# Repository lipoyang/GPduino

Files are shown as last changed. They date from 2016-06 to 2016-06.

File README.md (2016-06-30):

GPduino
=========

## 概要
GPduinoは、Arduino+Konashi互換のBLEラジコン制御ボードです。  
GPduinoに関する詳細は、[GPduino特設ページ](http://lipoyang.net/gpduino)をごらんください。  
GPduinoの回路/基板設計データとプリセットファームウェアのソースをここに公開します。

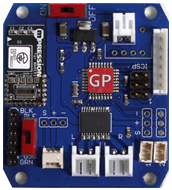
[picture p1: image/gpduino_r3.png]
GPduinoの写真
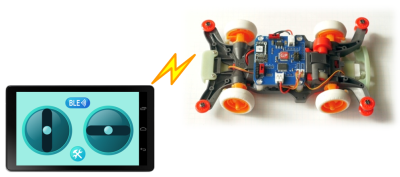
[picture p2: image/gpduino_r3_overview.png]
概要の図
　　　　　

## ファイル一覧

* firm/GPduinoR3/ : ファームウェア(Arduino Pro Mini 3.3V 互換のスケッチ)
* hard/GPduinoPCB/
	* GPduino.sch/brd: 回路/基板設計データ(Eagle形式)
	* GPduino.pdf: 回路図(PDF)
	* GPduino_BOM.xlsx: BOMリスト(Excel形式)
	* GPduino.GBL/GBO/GBP/GBS/GML/GTL/GTO/GTP/GTS/TXT: ガーバデータ
* LICENSE: Apache Licence 2.0です。
	* ただし、回路/基板設計は、Creative Commons Attribution Share-Alike 3.0です。
* README.md これ

## ブートローダの書き込み
部品実装したGPduino基板をArduinoとして使用できるようにするには、まずブートローダを書き込みます。
* ISPコネクタ（CN12）にISPプログラマーを接続します。向きに注意してください。
	* 3.3V系のArduino (Arduino Pro Mini 3.3V版など)をISPプログラマーにすることができます。
	* File > Examples > Arduino ISP をArduinoに書き込んでください。
* Arduino IDEにて、Tools > Board で、Arduino Pro or Pro Mini を選びます。
* Tools > Processor で、ATmega328(3.3V, 8MHz) を選びます。
* Tools > Programmer で、ISPプログラマーを選びます。
	* 上記の、Arduinoを使ったISPプログラマーの場合は、Arduino as ISPを選んでください。
* Tools > Burn Bootloader で、ブートローダーを書き込みます。

## ファームウェアの書き込み
GPduinoは、Arduino Pro Mini 3.3V版互換機です。
* 書き込みはArduino Pro Miniと同様、USBシリアル変換基板が必要です。CN13に接続してください。
	* SparkFun製 FTDI Basic Breakout - 3.3V を推奨します。かならず、3.3Vのものを使用してください。
* 基板のジャンパJ3を[USB]側に設定してください。
* Arduino IDEにて、Tools > Board で、Arduino Pro or Pro Mini を選びます。
* Tools > Processor で、ATmega328(3.3V, 8MHz) を選びます。
* Tools > Port で、USBシリアルのポート番号を選びます。
* Uploadボタンで、ファームウェアを書き込みます。

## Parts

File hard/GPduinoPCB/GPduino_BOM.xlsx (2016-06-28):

GPduino BOM
基板本体
No | Reference | Part Number | Vender | Description | DNP | Qty | Unit Price | Price | Lot Size | Supplier | Supplier Code
1 | C1 | 47u(3216) | (generic) | 3216型 |  | 1 | 30 | 30 | 10 | 秋月 | P-06040
2 | C2 | 10u(3216) | (generic) | 3216型 |  | 1 | 12.5 | 12.5 | 10 | 秋月 | P-06462
3 | C3,4,5,6,7 | 0.1u(1608) | (generic) | 1608型 |  | 4 | 0.325 | 1.3 | 4000 | 秋月 | P-01299
4 | CN1,2 | S2B-EH | JST | EH 2極 L型ポスト | DNP | 0 | 16 | 0 | 1 | 共立 | -
5 | CN3 | B6B-EH-A | JST | EH 6極 I型ポスト | DNP | 0 | 27 | 0 | 1 | 共立 | -
6 | CN4 | S2B-PH-K-S | JST | PH 2極 L型ポスト |  | 1 | 16 | 16 | 1 | 共立 | -
7 | CN5 | B4B-EH-A | JST | EH 4極 I型ポスト | DNP | 0 | 21 | 0 | 1 | 共立 | -
8 | CN6 | 53048-0310 | Molex | PicoBlade 3極 L型ポスト | DNP (部品は付属) | 1 | 45 | 45 | 5 | RS | 319-1092
9 | CN7,8 | 53047-0310 | Molex | PicoBlade 3極 I型ポスト | DNP | 0 | 29 | 0 | 5 | RS | 319-1064
10 | CN9 | - | (generic) | ピンヘッダ 3ピン | DNP (部品は付属) | 1 | 35 | 35 | 16 | 共立 | -
11 | CN10,11 | - | (generic) | ピンヘッダ 3ピン | DNP | 0 | 17 | 0 | 12 | 共立 | -
12 | CN12 | - | (generic) | ピンヘッダ 2×3ピン I型 | DNP | 0 | 70 | 0 | 1 | 共立 | -
13 | CN13 | 0 | (generic) | ピンヘッダ 6ピン I型 | DNP (部品は付属) | 1 | 70 | 70 | 8 | 共立 | -
14 | J3,SW1 | SS-12SDP2 | NKK | スライドスイッチ | DNP (部品は付属) | 2 | 66 | 132 | 1 | 共立 | 391139
15 | R1,2,3 | 10k(1608) | (generic) | 1608型 |  | 3 | 0.2 | 0.6 | 2500 | 秋月 | R-06103
16 | U1 | TC1262-3.3VDB05MP | Microchip | LDO, 3.3V-0.5A, SOT-223型 |  | 1 | 81 | 81 | 1 | RS | 703-7905
17 | U2 | TB6621FNG | Toshiba | Dual DCモータドライバ |  | 1 | 306 | 306 | 1 | RS | 770-3797
18 | U3 | ATmega328P-AU | Atmel | AVRマイコン |  | 1 | 367 | 367 | 1 | RS | 696-3092
19 | U4 | Koshian | Macnica | BLEモジュール |  | 1 | 980 | 980 | 1 | Macnica | -
20 | X1 | CSTCE8M00G55-R0 | Murata | セラロック 8MHz |  | 1 | 45 | 45 | 10 | RS | 721-4821
21 | - | - | FusionPCB | 基板 |  | 1 | 241.7 | 241.7 | 10 | FusionPCB | -
22 | - | PH2P300L | Marutsu | PH 2極 アッセンブルケーブル |  | 1 | 54 | 54 | 1 | マルツ | -
 |  |  |  |  |  |  | Total | 2417.1

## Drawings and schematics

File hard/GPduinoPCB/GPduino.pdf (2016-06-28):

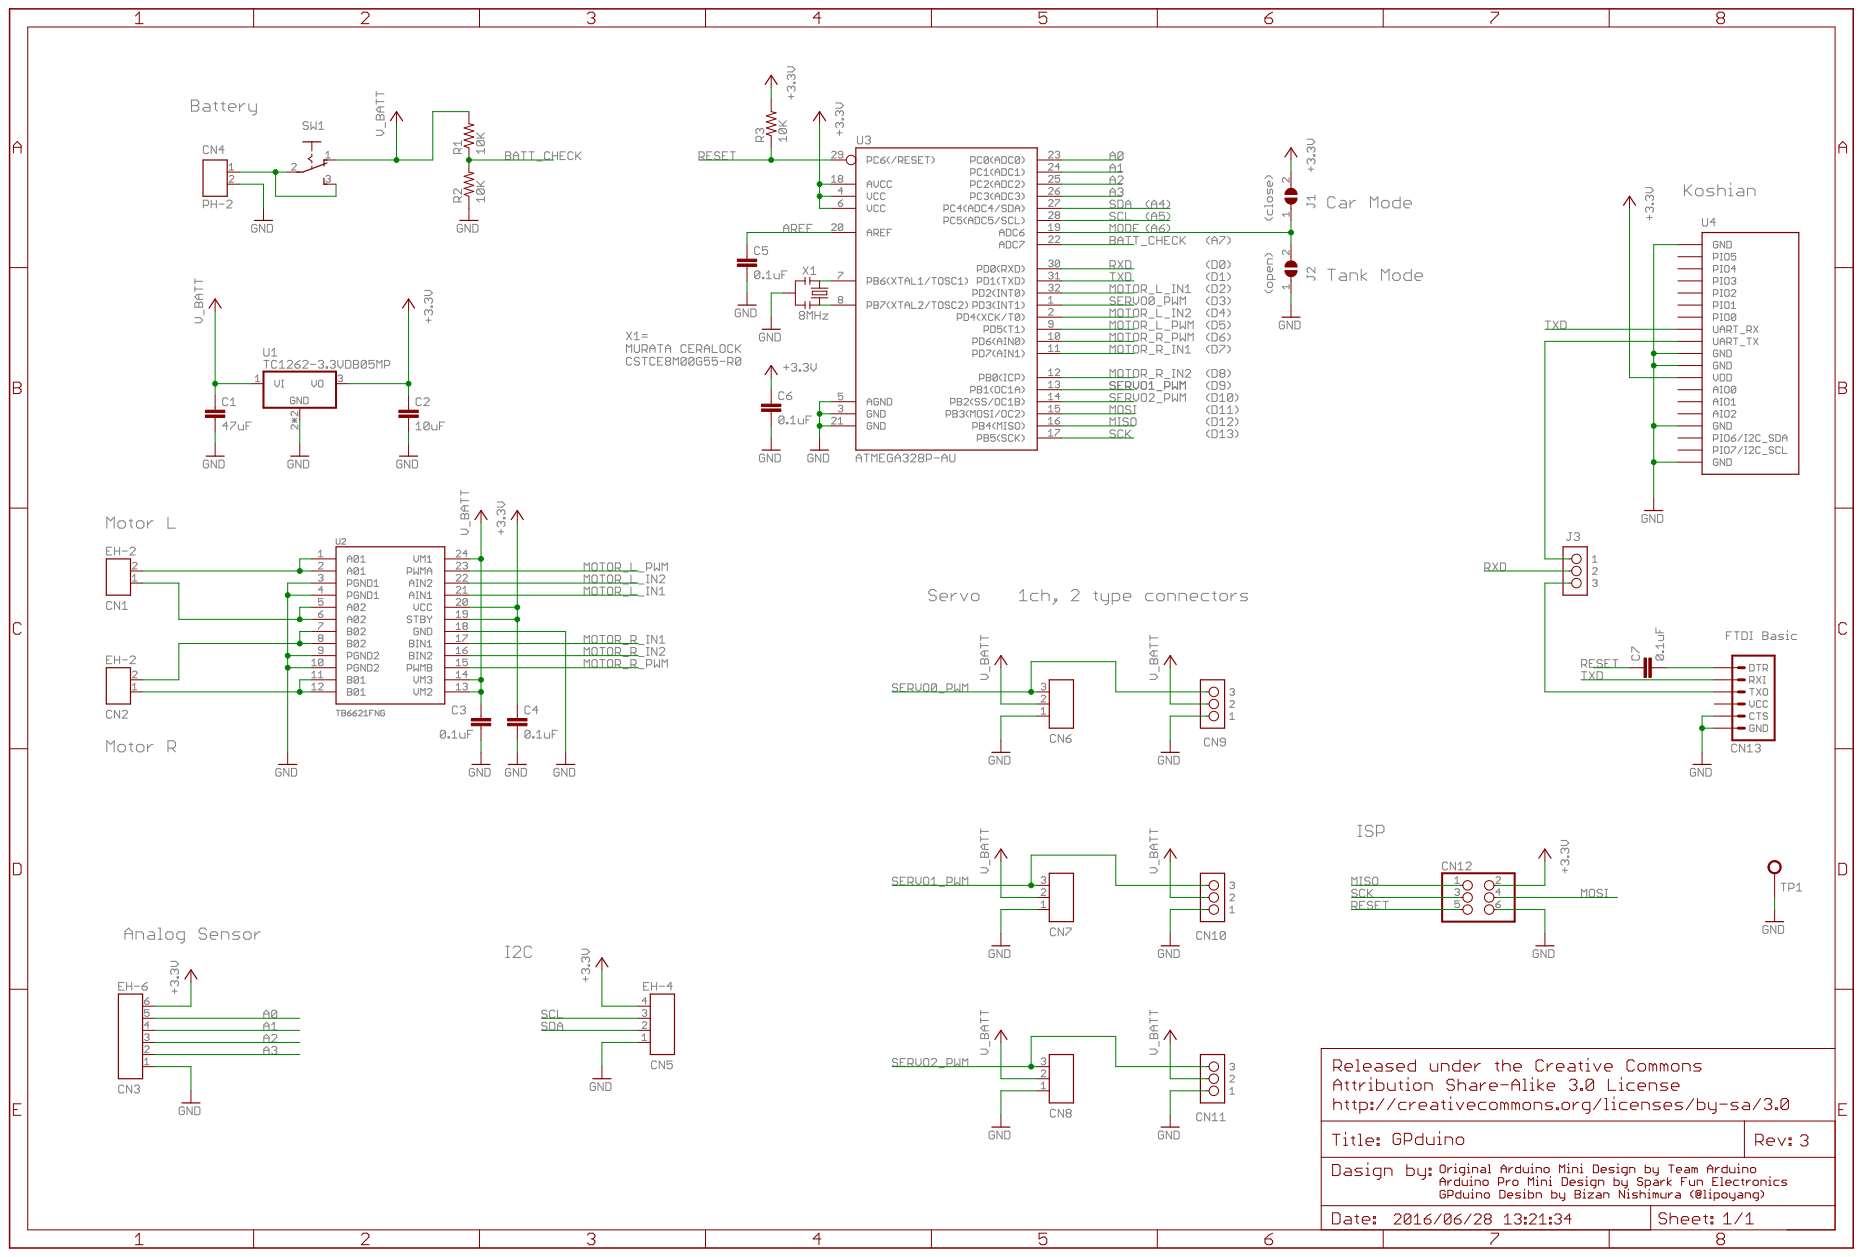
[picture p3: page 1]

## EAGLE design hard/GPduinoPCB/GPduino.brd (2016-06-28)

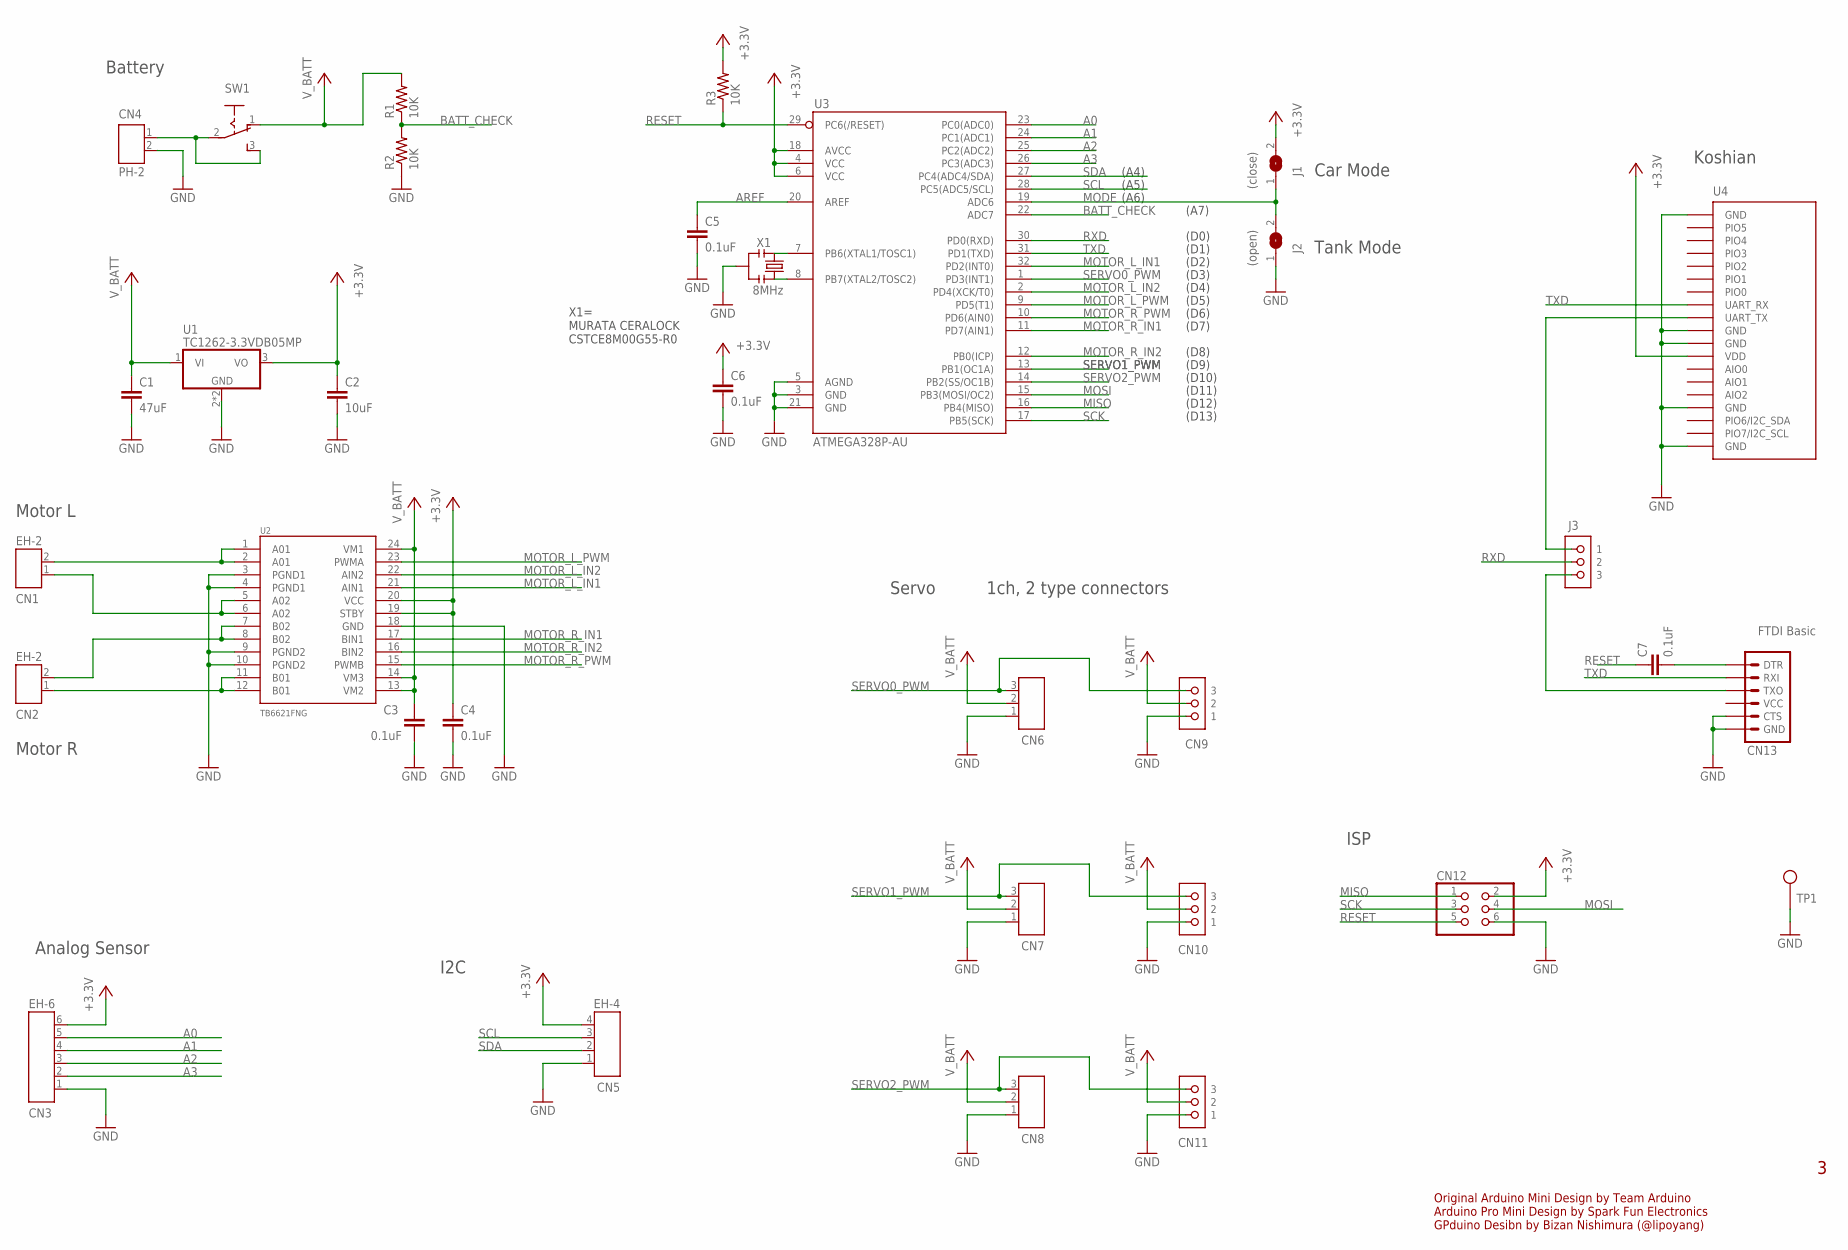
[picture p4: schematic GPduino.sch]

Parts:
C1: 47uF; C3216
C2: 10uF; C3216
C3, C4, C5, C6, C7: 0.1uF; C1608
CN1, CN2: EH-2
CN3: EH-6
CN4: PH-2
CN5: EH-4
CN6, CN7, CN8: PICOBLADE-3
CN9, CN10, CN11: cn6; CON_RC_SERVO
CN12: CN9; 2X03
CN13: FTDI Basic; 1X06
J1: (close); SJ
J2: (open); SJ
J3: XX-2; JUMPER_PIN_1X3
R1, R2, R3: 10K; 0603-RES
SW1: SW1; SLIDE-SW
TP1: TEST_PIN
U1: TC1262-3.3VDB05MP; SOT223
U2: TB6621FNG; SSOP24
U3: ATMEGA328P-AU; TQFP32-08
U4: KOSHIAN
X1: 8MHz; RESONATOR-SMD-1:1

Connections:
+3V3: C2.1, C4.1, C6.1, CN3.6, CN5.4, CN12.2, J1.2, R3.2, U1.3 (VO), U2.19 (STBY), U2.20 (VCC), U3.4 (VCC), U3.6 (VCC), U3.18 (AVCC), U4.12 (VDD)
A0: CN3.5, U3.23 (PC0(ADC0))
A01: CN1.2, U2.1 (A01), U2.2 (A01)
A1: CN3.4, U3.24 (PC1(ADC1))
A02: CN1.1, U2.5 (A02), U2.6 (A02)
A2: CN3.3, U3.25 (PC2(ADC2))
A3: CN3.2, U3.26 (PC3(ADC3))
AREF: C5.1, U3.20 (AREF)
BATT_CHECK: R1.1, R2.2, U3.22 (ADC7)
GND: C1.2, C2.2, C3.2, C4.2, C5.2, C6.2, CN3.1, CN4.2, CN5.1, CN6.1, CN7.1, CN8.1, CN9.1, CN10.1, CN11.1, CN12.6, CN13.5 (CTS), CN13.6 (GND), J2.1, R2.1, TP1.1, U1.2 (GND), U1.4 (GND), U2.3 (PGND1), U2.4 (PGND1), U2.9 (PGND2), U2.10 (PGND2), U2.18 (GND), U3.3 (GND), U3.5 (AGND), U3.21 (GND), U4.1 (GND), U4.10 (GND), U4.11 (GND), U4.16 (GND), U4.16@2 (GND), U4.20 (GND), X1.2
MISO: CN12.1, U3.16 (PB4(MISO))
MODE: J1.1, J2.2, U3.19 (ADC6)
MOSI: CN12.4, U3.15 (PB3(MOSI/OC2))
MOTOR_L_IN1: U2.21 (AIN1), U3.32 (PD2(INT0))
MOTOR_L_IN2: U2.22 (AIN2), U3.2 (PD4(XCK/T0))
MOTOR_L_PWM: U2.23 (PWMA), U3.9 (PD5(T1))
MOTOR_R_IN1: U2.17 (BIN1), U3.11 (PD7(AIN1))
MOTOR_R_IN2: U2.16 (BIN2), U3.12 (PB0(ICP))
MOTOR_R_PWM: U2.15 (PWMB), U3.10 (PD6(AIN0))
unnamed: CN4.1, SW1.2, SW1.3 (S)
unnamed: U3.8 (PB7(XTAL2/TOSC2)), X1.3
unnamed: U3.7 (PB6(XTAL1/TOSC1)), X1.1
unnamed: CN2.1, U2.11 (B01), U2.12 (B01)
unnamed: CN2.2, U2.7 (B02), U2.8 (B02)
unnamed: J3.1, U4.9 (UART_TX)
unnamed: C7.2, CN13.1 (DTR)
unnamed: CN13.3 (TXO), J3.3
RESET: C7.1, CN12.5, R3.1, U3.29 (PC6(/RESET))
RXD: J3.2, U3.30 (PD0(RXD))
SCK: CN12.3, U3.17 (PB5(SCK))
SCL: CN5.3, U3.28 (PC5(ADC5/SCL))
SDA: CN5.2, U3.27 (PC4(ADC4/SDA))
SERVO0_PWM: CN6.3, CN9.3, U3.1 (PD3(INT1))
SERVO1_PWM: CN7.3, CN10.3, U3.13 (PB1(OC1A))
SERVO2_PWM: CN8.3, CN11.3, U3.14 (PB2(SS/OC1B))
TXD: CN13.2 (RXI), U3.31 (PD1(TXD)), U4.8 (UART_RX), U4.8@2 (UART_RX)
V_BATT: C1.1, C3.1, CN6.2, CN7.2, CN8.2, CN9.2, CN10.2, CN11.2, R1.2, SW1.1 (O), U1.1 (VI), U2.13 (VM2), U2.14 (VM3), U2.24 (VM1)

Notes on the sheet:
Battery
Servo
Motor L
Original Arduino Mini Design by Team Arduino Arduino Pro Mini Design by Spark Fun Electronics GPduino Desibn by Bizan Nishimura (@lipoyang)
1ch, 2 type connectors
Analog Sensor
Motor R
ISP
Koshian
X1= MURATA CERALOCK CSTCE8M00G55-R0
Car Mode
Tank Mode
(D0)
(D1)
(D2)
(D3)
(D4)
(D5)
(D6)
(D7)
(D8)
(D9)
(D10)
(D11)
(D12)
(D13)
(A7)
(A6)
(A5)
(A4)
I2C

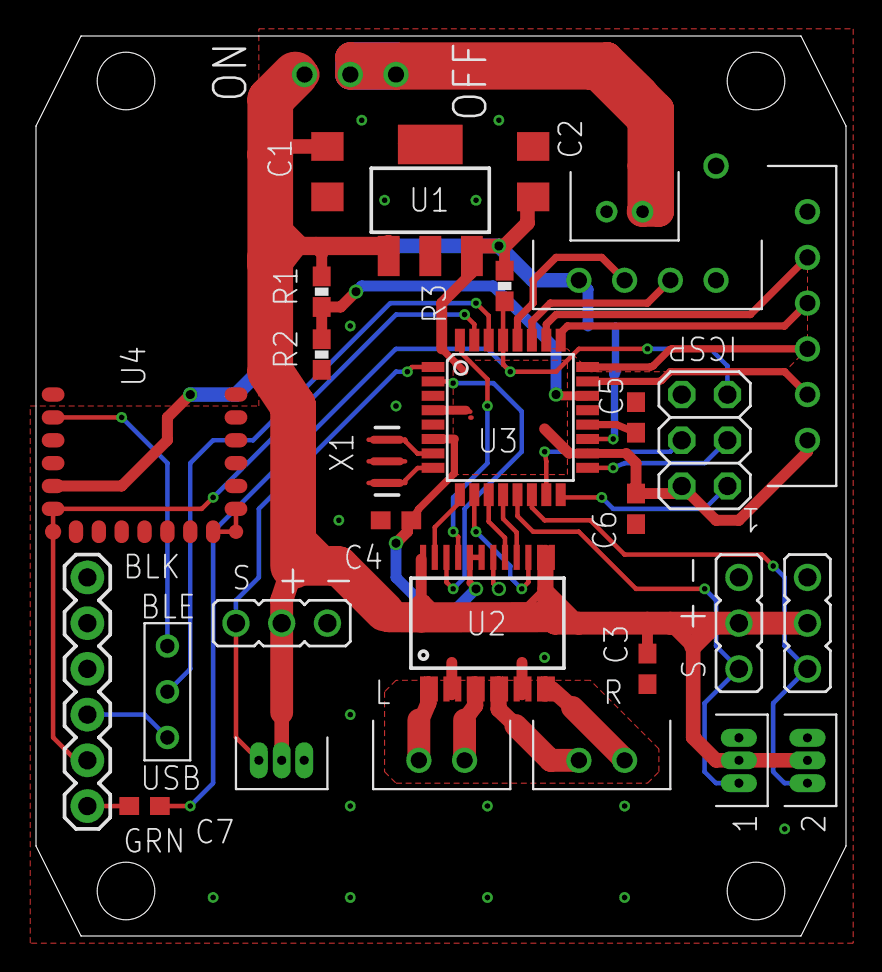
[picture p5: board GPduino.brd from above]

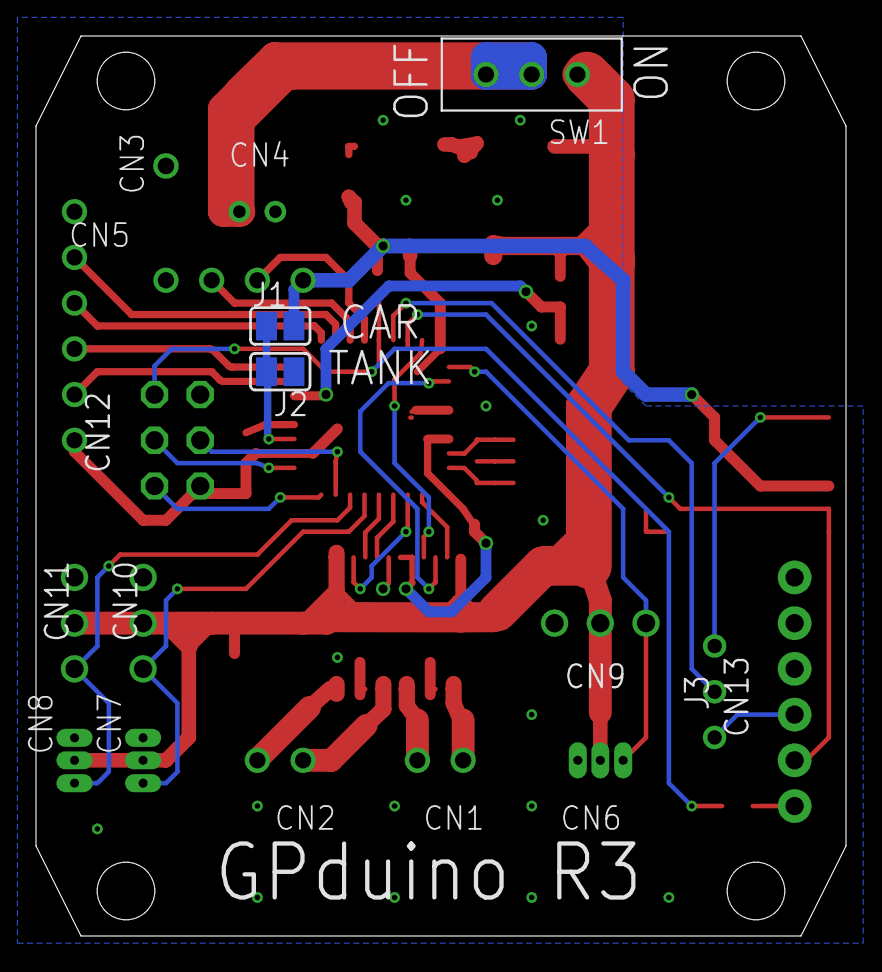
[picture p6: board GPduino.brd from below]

Board: 2 copper layers, 45.0 x 50.0 mm, 33 parts (3 on the bottom side), 37 nets.

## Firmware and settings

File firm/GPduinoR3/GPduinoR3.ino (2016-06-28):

/*
This software is available under NYSL(Nirunari Yakunari Sukinishiro License).
*/

#include <Servo.h>
#include <EEPROM.h>
#include "common.h"
#include "MovingAverage.h"

// ピン番号 (デジタル)
#define MOTOR_L_IN1    2
#define SERVO0_PWM     3
#define MOTOR_L_IN2    4
#define MOTOR_L_PWM    5
#define MOTOR_R_PWM    6
#define MOTOR_R_IN1    7
#define MOTOR_R_IN2    8
#define SERVO1_PWM     9
#define SERVO2_PWM     10

// ピン番号 (アナログ)
#define ANALOG_0      0
#define ANALOG_1      1
#define ANALOG_2      2
#define ANALOG_3      3
#define MODE_CHECK    6
#define BATT_CHECK    7

// サーボ
Servo servo[3];

// バッテリー電圧チェック
MovingAverage Vbat_MovingAve;

// モード
static int drive_mode;
#define MODE_TANK   0   // 戦車モード
#define MODE_CAR    1   // 自動車モード

// 戦車モードのプロポ状態保持用
static int g_fb;  // 前後方向
static int g_lr;  // 左右方向

// 暴走チェックカウンタ
static int cnt_runaway;

// 3.3V未満でローバッテリーとする
// (3.3V / 2) / 3.3V * 1024 =  512
#define LOW_BATTERY    512

// 四輪操舵のモード
static int g_steer_pol_f;
static int g_steer_pol_b;

// サーボの調整
static int g_servo_pol[3]; // 極性
static int g_servo_ofs[3]; // オフセット
static int g_servo_amp[3]; // 振幅

// 送信バッファ
static char txbuff[256];

/**
 * バッテリー電圧チェック
 */
void battery_check()
{
    static int cnt = 0;
    
    unsigned short Vbat = analogRead(BATT_CHECK);
    unsigned short Vbat_ave = Vbat_MovingAve.pop(Vbat);
    
    // 1秒ごとに電圧値送信
    cnt++;
    if(cnt >= 1000)
    {
        cnt=0;
        
        txbuff[0]='#';
        txbuff[1]='B';
        Uint16ToHex(&txbuff[2], Vbat_ave, 3);
        txbuff[5]='$';
        txbuff[6]='\0';
        Serial.print(txbuff);
    }
    
    // 電圧が低下したら停止
    if(Vbat_ave < LOW_BATTERY){
        // モータ停止
        analogWrite(MOTOR_L_PWM, 0);
        analogWrite(MOTOR_R_PWM, 0);
        digitalWrite(MOTOR_L_IN1, LOW);
        digitalWrite(MOTOR_L_IN2, LOW);
        digitalWrite(MOTOR_R_IN1, LOW);
        digitalWrite(MOTOR_R_IN2, LOW);
        // 復帰しない
        while(true){
            ;
        }
    }
}

/**
 * 暴走チェック
 */
void runaway_check()
{
    cnt_runaway++;
    
    // 1秒間コマンドが来なければモータ停止
    if(cnt_runaway > 1000)
    {
      analogWrite(MOTOR_L_PWM, 0);
      analogWrite(MOTOR_R_PWM, 0);
      digitalWrite(MOTOR_L_IN1, LOW);
      digitalWrite(MOTOR_L_IN2, LOW);
      digitalWrite(MOTOR_R_IN1, LOW);
      digitalWrite(MOTOR_R_IN2, LOW);
    }
}

/*
 * サーボの初期化
 */
void servo_init()
{
    int i;
    if(EEPROM.read(0) == 0xA5){
        for(i=0;i<3;i++){
            g_servo_pol[i] = (int)((signed char)EEPROM.read(i*3 + 1));
            g_servo_ofs[i] = (int)((signed char)EEPROM.read(i*3 + 2));
            g_servo_amp[i] =                    EEPROM.read(i*3 + 3);
        }
    }else{
        EEPROM.write(0, 0xA5);
        for(i=0;i<3;i++){
            g_servo_pol[i] = 1;
            g_servo_ofs[i] = 0;
            g_servo_amp[i] = 90;
            EEPROM.write(i*3 + 1, g_servo_pol[i]);
            EEPROM.write(i*3 + 2, g_servo_ofs[i]);
            EEPROM.write(i*3 + 3, g_servo_amp[i]);
        }
    }
    servo[0].attach(SERVO0_PWM);
    servo[1].attach(SERVO1_PWM);
    servo[2].attach(SERVO2_PWM);
    servo_ctrl(0,0);
    servo_ctrl(1,0);
    servo_ctrl(2,0);
}

/*
 * サーボ制御
 */
void servo_ctrl(int ch, int val)
{
    int deg = 90 + ((val + g_servo_ofs[ch]) *  g_servo_amp[ch]) / 127 * g_servo_pol[ch];
    
    // sprintf(txbuff, "%4d %4d / %4d %4d %4d", val, deg, g_servo_ofs[ch], g_servo_amp[ch], g_servo_pol[ch]);
    // Serial.println(txbuff);
    
    servo[ch].write(deg);
}

// 初期設定
void setup() {
    // シリアル通信の設定
    SerialCom_init();

    // PWMの初期化
    analogWrite(MOTOR_L_PWM, 0);
    analogWrite(MOTOR_R_PWM, 0);
    
    // GPIOの初期化
    digitalWrite(MOTOR_L_IN1, LOW);
    digitalWrite(MOTOR_L_IN2, LOW);
    digitalWrite(MOTOR_R_IN1, LOW);
    digitalWrite(MOTOR_R_IN2, LOW);
    pinMode(MOTOR_L_IN1, OUTPUT);
    pinMode(MOTOR_L_IN2, OUTPUT);
    pinMode(MOTOR_R_IN1, OUTPUT);
    pinMode(MOTOR_R_IN2, OUTPUT);
    
    // モード判定
    int mode_check = analogRead( MODE_CHECK );
    drive_mode = (mode_check > 512) ? MODE_CAR : MODE_TANK;

    if(drive_mode == MODE_CAR){
        // サーボの初期化
        servo_init();
    }
    
    // 変数初期化
    g_fb = 0;
    g_lr = 0;
    cnt_runaway = 0;
    Vbat_MovingAve.init();
    g_steer_pol_f = 1;
    g_steer_pol_b = 0;
}

// メインループ
void loop() {
    
    // シリアル受信
    SerialCom_loop();
    // バッテリー電圧チェック
    battery_check();
    // 暴走チェック
    runaway_check();
    
    delay(1);
}

/*
 * モータの制御
 */
void ctrl_motor(int ch, int val)
{
    static const int IN1[]={MOTOR_L_IN1, MOTOR_R_IN1};
    static const int IN2[]={MOTOR_L_IN2, MOTOR_R_IN2};
    static const int PWM[]={MOTOR_L_PWM, MOTOR_R_PWM};
    
    int l,r;
    int lpwm,rpwm,lin1,lin2,rin1,rin2;
    
    int pwm = (abs(val) << 1) + 1;
    if(pwm<0) pwm = 0;
    if(pwm>255) pwm = 255;
    
    int in1,in2;
    if(val > 0){
        in1 = LOW;
        in2 = HIGH;
    }else if(val < 0){
        in1 = HIGH;
        in2 = LOW;
    }else{
        in1 = LOW;
        in2 = LOW;
        pwm = 0;
    }

    digitalWrite(IN1[ch], in1);
    digitalWrite(IN2[ch], in2);
    analogWrite(PWM[ch], pwm);
}

/**
 * 戦車のモータ制御
 */
void ctrl_tank()
{
    int l,r;
    int lpwm,rpwm,lin1,lin2,rin1,rin2;
    
    r = (int)(g_fb - g_lr/2);
    l = (int)(g_fb + g_lr/2);
    
    // sprintf(txbuff, "%4d %4d %4d %4d", l, r, g_fb, g_lr);
    // Serial.println(txbuff);
    
    ctrl_motor(0, l);
    ctrl_motor(1, r);
}

/**
 * 受信したコマンドの実行
 *
 * @param buff 受信したコマンドへのポインタ
 */
void SerialCom_callback(char* buff)
{
    unsigned short val;
    int sval, sval2;
    int deg;
    int ch;
    int i;
    
    cnt_runaway = 0; // 暴走チェックカウンタのクリア
    
    // Serial.println(buff); // TEST
    
    switch(buff[0])
    {
    /* Dコマンド(前進/後退)
       書式: #Dxx$
       xx: 0のとき停止、正のとき前進、負のとき後退。
     */
    case 'D':
        // 値の解釈
        if( HexToUint16(&buff[1], &val, 2) != 0 ) break;
        sval = (int)((signed char)val);
        
        // 自動車モードの場合
        if(drive_mode == MODE_CAR)
        {
            ctrl_motor(0, sval);
            ctrl_motor(1, sval);
        }
        // 戦車モードの場合
        else
        {
            g_fb = sval;
            ctrl_tank();
        }
        break;
        
    /* Tコマンド(旋回)
       書式: #Txxn$
       n: 4WSモード。0のとき後輪固定、1のとき同相、2のとき逆相
       xx: 0のとき中立、正のとき右旋回、負のとき左旋回
     */
    case 'T':
        // 4WSモード
        switch(buff[3]){
        case '0':// FRONT
            g_steer_pol_f = 1;
            g_steer_pol_b = 0;
            break;
        case '1':// COMMON
            g_steer_pol_f = 1;
            g_steer_pol_b = 1;
            break;
        case '2':// REVERSE
            g_steer_pol_f = 1;
            g_steer_pol_b = -1;
            break;
        case '3':// REAR
            g_steer_pol_f = 0;
            g_steer_pol_b = 1;
            break;
        default:
            g_steer_pol_f = 1;
            g_steer_pol_b = 0;
            break;
        }
        // 値の解釈
        if( HexToUint16(&buff[1], &val, 2) != 0 ) break;
        sval = (int)((signed char)val);
        
        // 自動車モードの場合
        if(drive_mode == MODE_CAR)
        {
            servo_ctrl(0, sval);
            servo_ctrl(1, g_steer_pol_f * sval);
            servo_ctrl(2, g_steer_pol_b * sval);
        }
        // 戦車モードの場合
        else
        {
            g_lr = sval;
            ctrl_tank();
        }
        break;
        
    /* Mコマンド(モータ制御)
       書式1: #Mnxx$
       n: '1'はモータ1(左)、'2'はモータ2(右)
       xx: 0のとき停止、正のとき正転、負のとき反転
       
       書式2: #MAxxyy$
       xx: モータ1(左)  0のとき停止、正のとき正転、負のとき反転
       yy: モータ2(右)  0のとき中立、正のとき正転、負のとき反転
     */
    case 'M':
        switch(buff[1]){
        case '1':
            // 値の解釈
            if( HexToUint16(&buff[2], &val, 2) != 0 ) break;
            sval = (int)((signed char)val);
            ctrl_motor(0, sval);
            break;
        case '2':
            // 値の解釈
            if( HexToUint16(&buff[2], &val, 2) != 0 ) break;
            sval = (int)((signed char)val);
            ctrl_motor(1, sval);
            break;
        case 'A':
            // 値の解釈
            if( HexToUint16(&buff[2], &val, 2) != 0 ) break;
            sval = (int)((signed char)val);
            if( HexToUint16(&buff[4], &val, 2) != 0 ) break;
            sval2 = (int)((signed char)val);
            ctrl_motor(0, sval);
            ctrl_motor(1, sval2);
            break;
        }
        break;
        
    /* Sコマンド(サーボ制御)
       書式: #Sxxn$
       xx: 0のとき中立、正のとき正転、負のとき反転
       n: サーボチャンネル 0～2
     */
    case 'S':
        // 値の解釈
        if( HexToUint16(&buff[1], &val, 2) != 0 ) break;
        sval = (int)((signed char)val);
        // チャンネル
        ch = (buff[3] == '1') ? 1 : ((buff[3] == '2') ? 2 : 0);
        // サーボの制御
        servo_ctrl(ch, sval);
        break;
        
    /* Aコマンド(サーボの調整)
        (1)サーボ極性設定
           書式: #APxn$
           n: サーボチャンネル 0～2
           xは'+'または'-'。'+'は正転、'-'は反転。初期値は正転。
        (2)サーボオフセット調整
           書式: #AOxxn$
           n: サーボチャンネル 0～2
           xx:中央位置のオフセット
        (3)サーボ振幅調整
           書式: #AAnxx$
           n: サーボチャンネル 0～2
           xx:振れ幅
        (4)サーボ設定値保存
           書式: #AS$
           サーボの設定値をEEPROMに保存する
        (5)サーボ設定値読み出し
            書式: #AL$
           サーボの設定値をEEPROMから読み出し、送信する
     */
    case 'A':
        switch(buff[1]){
        case 'P':
            ch = (buff[3] == '1') ? 1 : ((buff[3] == '2') ? 2 : 0);
            if(buff[2] == '+'){
                g_servo_pol[ch] = 1;
            }else if(buff[2] == '-'){
                g_servo_pol[ch] = -1;
            }
            break;
        case 'O':
            ch = (buff[4] == '1') ? 1 : ((buff[4] == '2') ? 2 : 0);
            // 値の解釈
            if( HexToUint16(&buff[2], &val, 2) != 0 ) break;
            g_servo_ofs[ch] = (int)((signed char)val);
            break;
        case 'A':
            ch = (buff[4] == '1') ? 1 : ((buff[4] == '2') ? 2 : 0);
            // 値の解釈
            if( HexToUint16(&buff[2], &val, 2) != 0 ) break;
            g_servo_amp[ch] = (int)((unsigned char)val);
            break;
        case 'S':
            for(i=0;i<3;i++){
                EEPROM.write(i*3 + 1, g_servo_pol[i]);
                EEPROM.write(i*3 + 2, g_servo_ofs[i]);
                EEPROM.write(i*3 + 3, g_servo_amp[i]);
            }
            break;
        case 'L':
            //delay(200); // バッファ詰まりの応急処置 (よろしくない)
            txbuff[0]='#';
            txbuff[1]='A';
            txbuff[2]='L';
            for(i=0;i<3;i++){
                g_servo_pol[i] = (int)((signed char)EEPROM.read(i*3 + 1));
                g_servo_ofs[i] = (int)((signed char)EEPROM.read(i*3 + 2));
                g_servo_amp[i] =                    EEPROM.read(i*3 + 3);
                txbuff[3+i*5] = (g_servo_pol[i]==1) ? '+' : '-';
                Uint16ToHex(&txbuff[4+i*5], (unsigned short)((unsigned char)g_servo_ofs[i]), 2);
                Uint16ToHex(&txbuff[6+i*5], (unsigned short)(               g_servo_amp[i]), 2);
            }
            txbuff[18]='$';
            txbuff[19]='\0';
            Serial.print(txbuff);
            //delay(200); // バッファ詰まりの応急処置 (よろしくない)
            break;
        }
        break;
    }
}

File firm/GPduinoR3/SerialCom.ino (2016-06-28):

/*
This software is available under NYSL(Nirunari Yakunari Sukinishiro License).
*/

// シリアルコマンド電文の受信処理

// 0x02/0x03だとデバッグしにくいので、#/$ を 電文開始/終了 に使う
// 電文開始
#define CODE_STX '#'
// 電文終了
#define CODE_ETX '$'

// 受信状態
static int state;
// 電文開始待ち状態
#define STATE_READY     0
// 電文受信中状態
#define STATE_RECEIVING 1

// 受信バッファ
#define BUFF_SIZE 32
static int ptr=0;
static char buff[BUFF_SIZE];

// 受信コマンド処理
extern void SerialCom_callback(char* buff);

// 初期化
void SerialCom_init()
{
    state = STATE_READY;
    
    // シリアル通信の設定
//  Serial.begin(9600);
//  Serial.begin(19200);
    Serial.begin(38400);
}


// 受信ループ処理
void SerialCom_loop() {

    char c;
    
    /* シリアル受信データがあるか？ */
    while (Serial.available() > 0)
    {
        //Serial.println("RECV ");
        c = Serial.read();
        switch(state)
        {
        /* 電文開始待ち状態 */
        case STATE_READY:
            /* 電文開始コードが来たら電文受信中状態へ */
            if(c == CODE_STX)
            {
                //Serial.println("STX ");
                state = STATE_RECEIVING;
                ptr = 0;
            }
            break;
        /* 電文受信中状態 */
        case STATE_RECEIVING:
            /* もしも電文開始コードが来たら受信中のデータを破棄 */
            if(c == CODE_STX)
            {
                //Serial.println("STX ");
                ptr = 0;
            }
            /* 電文終了コードが来たら、受信した電文のコマンドを実行 */
            else if(c == CODE_ETX)
            {
                //Serial.println("ETX ");
                buff[ptr] = '\0';
                SerialCom_callback(buff);
                state = STATE_READY;
            }
            /* 1文字受信 */
            else
            {
                buff[ptr] = c;
                ptr++;
                if(ptr>=BUFF_SIZE)
                {
                    state = STATE_READY;
                }
            }
            break;
        default:
            state = STATE_READY;
        }
    }
}

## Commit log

2016-06-28 ファイル追加
    [GPduino.GBL, GPduino.GBO, GPduino.GBP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]
2016-06-29 READMEの追記

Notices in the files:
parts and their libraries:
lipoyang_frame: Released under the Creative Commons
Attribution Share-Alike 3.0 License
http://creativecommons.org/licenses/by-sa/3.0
